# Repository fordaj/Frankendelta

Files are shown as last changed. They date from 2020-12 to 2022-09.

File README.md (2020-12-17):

# Frankendelta
Meet the 45lb, reassembled many times, absolute unit of a Delta 3D Printer: Frankendelta.
~Picture goes here~
Over the summer of 2019, my dad and I worked together to design a 3D printer with a build volume large enough to print my head (that wasn't the main goal... but it's on the list). In all fairness, my dad brought in most of the expertise from building his Kossel Mini Delta 3D printer, scaling up the things he felt worked well from that. I had experience with cartesian printers, but deltas are a different beast. With the right settings, they can print extremely quickly without quality loss due to their light effectors. This repository serves as a medium for functionality and documentation, where I can refer back to the processes and files used to get Frankendelta humming and happy as needed.

## Parts List
Here are most of the parts included in this build. Some not included are the aluminum sheets my dad milled on his CNC, T-nuts, control board standoffs, fans, and supplies (wires, JTX connectors, solder, cables, fuses, etc.). All in all, ended up costing ~$800.
| Quantity | Type | Item | Price |
|--|--|--|--|
| 1 | Control Board | [BIGTREETECH SKR V1.3 32-bit Smoothie Board with SPI TMC2130 Stepper Drivers](https://www.biqu.equipment/products/pre-sale-bigtreetech-skr-v1-3-smoothieboard-32-bit-open-source-arm-cpu-motherboard-support-uart-model-2004lcd-3d-printer-parts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) | $44.95 |
| 1 | Power Supply | [Meanwell 24V, 200W PSU](https://www.aliexpress.com/item/32855960682.html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,searchweb201602_9_10065_10130_10068_10890_10547_319_10546_317_10548_10545_10696_453_10084_454_10083_10618_10307_537_536_10059_10884_10887_321_322_10103,searchweb201603_35,ppcSwitch_0&algo_expid=8e751027-f404-431d-9236-467e57eb0355-0&algo_pvid=8e751027-f404-431d-9236-467e57eb0355&transAbTest=ae803_3) | $32.30 |
| 1 | LCD | [MKS 12864LCD](https://www.amazon.com/HiLetgo-Printer-Controller-Display-Arduino/dp/B07X378P8X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) | $12.99 |
| 4 | Stepper Motors | [NEMA 17 0.9 deg 76oz.in Steppers](https://www.seemecnc.com/collections/parts-accessories/products/nema-17-stepper-motor-1-8-degree-76oz-in-2a-5mm-shaft-w-flat) | $22.50 |
| 7 | Belts | [GT2 x 6mm Wide Timing Belt (sold per meter)](https://www.seemecnc.com/collections/parts-accessories/products/gt2-timing-belt) | $45.50 |
| 1 | Bed Heater| [Circular Silicone Bed Heater 120v, 300mm, 350W](https://www.seemecnc.com/collections/parts-accessories/products/silicone-heater-for-300mm-diameter-beds) | $40.00 |
| 1 | Build Plate | [310mm Circular Glass Build Plate](https://www.seemecnc.com/collections/parts-accessories/products/boroscillicate-glass-build-plate-310mm) | $30.00 |
| 1 | Extruder | [EZR Struder](https://www.seemecnc.com/collections/parts-accessories/products/ezrstruder) | $35.00 |
| 1 | Relay | [Solid State Relay (SSR) 24V~480VAC, 40A, 3-32VDC Control](https://docs.google.com/spreadsheets/d/126paPdKw47GO45m8PfAj-qZeEyYEzkp5sGYM6t5eCeo/edit#gid=2045847217) | $25.00 |
| 3 | Timing Pulley | [16 Tooth Timing Pulley for GT2 x 6mm Belt](https://www.seemecnc.com/collections/parts-accessories/products/16-tooth-g-series-2mm-pitch-x-6mm-wide-timing-pulley-3-pack) | $3.50 |
| 1 | Bed Thermistor | [100k Glass Bead NTC Thermistor](https://www.seemecnc.com/collections/parts-accessories/products/thermistor-100k-ntc) | $6.00 |
| 1 | PTFE Tube | [2mm ID x 4mm OD PTFE Tubing, 7ft](https://www.seemecnc.com/collections/parts-accessories/products/ptfe-tubing-2mm-id-x-4mm-od) | $2.70 |
| 1 | Kossel Delta Corners | [2040 Aluminum Alloy Delta Angle Corner Kit, Kossel XL Update](https://www.aliexpress.com/item/32811135341.html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,searchweb201602_9_10065_10130_10068_10890_10547_319_10546_317_10548_10545_10696_453_10084_454_10083_10618_10307_537_536_10059_10884_10887_321_322_10103,searchweb201603_35,ppcSwitch_0&algo_expid=a3b4f901-13f0-4ec3-b1fd-ec0813078da3-0&algo_pvid=a3b4f901-13f0-4ec3-b1fd-ec0813078da3&transAbTest=ae803_3) | $63.99 |
| 3 | Linear Rails | [600mm MGN9 C Linear Rails with Sliding Carriage](https://www.aliexpress.com/item/3D-print-parts-cnc-Kossel-Mini-MGN9-9mm-miniature-linear-rail-slide-1pc-MGN9-linear-rail/32806622073.html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,searchweb201602_9_10065_10130_10068_10890_10547_319_10546_317_10548_10545_10696_453_10084_454_10083_10618_10307_537_536_10059_10884_10887_321_322_10103,searchweb201603_35,ppcSwitch_0&algo_expid=1050dd04-ff44-4791-b0d4-8a9743b34de0-0&algo_pvid=1050dd04-ff44-4791-b0d4-8a9743b34de0&transAbTest=ae803_3) | $59.49 |
| 1 | Probe | [Duet IR Auto-Bed Leveling Probe](https://www.printedsolid.com/products/duet-ir-probe) | $24.85 |
| 1 | Hotend | [E3D V6 24V Bowden All-Metal Hotend](https://e3d-online.com/collections/hotends/products/v6-all-metal-hotend) | $53.50 |
| 1 | Linear Rails | [V-Slot 20mm x 60mm x 500mm Linear Rail, Black](https://openbuildspartstore.com/v-slot-20x60-linear-rail/) | $10.99 |
| 3 | Linear Rails | [V-Slot 20mm x 40mm x 1000mm Linear Rail, Black](https://openbuildspartstore.com/v-slot-20x40-linear-rail/) | $45.87 |
| 3 | Linear Rails | [V-Slot 20mm x 40mm x 500mm Linear Rail, Black](https://openbuildspartstore.com/v-slot-20x40-linear-rail/) | $23.97 |
| 3 | Linear Rails | [V-Slot 20mm x 40mm x 500mm Linear Rail, Black](https://openbuildspartstore.com/v-slot-20x20-linear-rail/) | $17.97 |

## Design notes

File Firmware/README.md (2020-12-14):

# Marlin Firmware
[Marlin firmware](https://marlinfw.org) version 2.0.7.2, last built 12-14-2020 in [firmware.bin](firmware.bin)

## Configuration.h
All of the changes I've made to the [Configuration.h](Marlin/Configuration.h) file. Since I am using a delta printer, I started with the generic example in [Marlin's configuration repository](https://github.com/MarlinFirmware/Configurations). Sections correspond with order of appearance in files. Actual code shown for simpler CTRL+f navigation.

### Setup
Shows up on host during boot and M115
```cpp
#define STRING_CONFIG_H_AUTHOR "Andrew Ford"
```
Default to serial port 0, otherwise emulate
```cpp
#define SERIAL_PORT 0
#define SERIAL_PORT_2 -1
```
Define motherboard (using BigTreeTech SKR V1.3)
```cpp
#define MOTHERBOARD BOARD_BTT_SKR_V1_3
```
Set printer name
```cpp
#define CUSTOM_MACHINE_NAME "Frankendelta"
```
Disable power supply unit control
```cpp
//#define PSU_CONTROL
```

### Thermistors
Hotend thermistor selection
```cpp
#define TEMP_SENSOR_0 5
```
Bed thermistor selection
```cpp
#define TEMP_SENSOR_BED 1
```

### PID Settings
Auto-tune menu on LCD
```cpp
#define PID_AUTOTUNE_MENU
```
Since I only have 1 hotend, I can set global PID settings
```cpp
#define DEFAULT_Kp 24.43
#define DEFAULT_Ki 1.93
#define DEFAULT_Kd 77.53
```
Use PID settings for bed. Limit heating so that adhesive doesn't melt
```cpp
#define PIDTEMPBED

#define MAX_BED_POWER 200

#define DEFAULT_bedKp 164.97
#define DEFAULT_bedKi 27.02
#define DEFAULT_bedKd 671.52
```

### Delta Settings
After homing, move downwards to prevent overshooting homing sensors
```cpp
#define DELTA_HOME_TO_SAFE_ZONE
```
Allow user to define safe zone
```cpp
#define DELTA_CALIBRATION_MENU
```
Allow G33 Auto-Calibration (used in [calibration file](https://github.com/fordaj/Frankendelta/blob/main/Calibration/calibrateDelta.gcode))
```cpp
#define DELTA_AUTO_CALIBRATION
```
Printable radius(mm) = diameter/2 - unreachable space
```cpp
#define DELTA_PRINTABLE_RADIUS 150.0
```
Diagonal push-rod length
```cpp
#define DELTA_DIAGONAL_ROD 360.24 
```
Printable height (obtained from [calibration file](https://github.com/fordaj/Frankendelta/blob/main/Calibration/calibrateDelta.gcode))
```cpp
#define DELTA_HEIGHT 535.26
```
Endstop adjustment (obtained from [calibration file](https://github.com/fordaj/Frankendelta/blob/main/Calibration/calibrateDelta.gcode))
```cpp
#define DELTA_ENDSTOP_ADJ { 0.0, -0.26, -2.10 }
```
Diagonal push-rod horizontal coverage with centered effector(obtained from [calibration file](https://github.com/fordaj/Frankendelta/blob/main/Calibration/calibrateDelta.gcode))
```cpp
#define DELTA_RADIUS 186.95
```
Tower angle trim
```cpp
#define DELTA_TOWER_ANGLE_TRIM { 0.24, -0.10, -0.14 }
```
Delta radius/diagonal rod adjustments
```cpp
#define DELTA_DIAGONAL_ROD_TRIM_TOWER { 0.0, 0.0, 0.0 }
```

### Endstop Settings
Disable endstop pullups
```cpp
//#define ENDSTOPPULLUPS
```
Ensure endstops are non-inverting
```cpp
#define X_MIN_ENDSTOP_INVERTING false
#define Y_MIN_ENDSTOP_INVERTING false
#define Z_MIN_ENDSTOP_INVERTING false
#define X_MAX_ENDSTOP_INVERTING false
#define Y_MAX_ENDSTOP_INVERTING false
#define Z_MAX_ENDSTOP_INVERTING false
#define Z_MIN_PROBE_ENDSTOP_INVERTING false
```
Enable stepper drivers
```cpp
#define X_DRIVER_TYPE  TMC2130
#define Y_DRIVER_TYPE  TMC2130
#define Z_DRIVER_TYPE  TMC2130

#define E0_DRIVER_TYPE TMC2130
```

### Movement Settings
Adjust "Axis Steps Per Unit" variables
```cpp
#define XYZ_FULL_STEPS_PER_ROTATION 400

#define XYZ_PULLEY_TEETH 16

#define DEFAULT_AXIS_STEPS_PER_UNIT { DEFAULT_XYZ_STEPS_PER_UNIT, DEFAULT_XYZ_STEPS_PER_UNIT, DEFAULT_XYZ_STEPS_PER_UNIT, 158 } 
```
Increase max hotend feedrate
```cpp
#define DEFAULT_MAX_FEEDRATE { 500, 500, 500, 150 }
```
Lower default acceleration
```cpp
#define DEFAULT_ACCELERATION 2000
```
Change default hotend jerk
```cpp
#define DEFAULT_ACCELERATION 2000
```

### Z-Probe Options
Since we are using a laser probe, no mechanical deployment is needed
```cpp
#define FIX_MOUNTED_PROBE
```
Adjust nozzle-to-probe offset
```cpp
#define NOZZLE_TO_PROBE_OFFSET { 0, -19, -2.40 }
```
Define gap between probe locations and bed edge
```cpp
#define PROBING_MARGIN 40
```
Set probe XY movement speed to 100mm/s
```cpp
#define XY_PROBE_SPEED (100*60)
```
Enable multi-probing for improved accuracy
```cpp
#define MULTIPLE_PROBING 2
```
Adjust z-clearances
```cpp
#define Z_CLEARANCE_DEPLOY_PROBE   20
#define Z_CLEARANCE_BETWEEN_PROBES  8
#define Z_CLEARANCE_MULTI_PROBE     5
```
Enable minimum software endstops
```cpp
#define MIN_SOFTWARE_ENDSTOPS
```

### Bed Leveling
Enable 3-point bed leveling since I have a glass bed
```cpp
#define AUTO_BED_LEVELING_3POINT
```
If there is bed level data stored, load it after every [bed leveling](https://github.com/fordaj/Frankendelta/blob/main/Calibration/levelBed.gcode)
```cpp
#define RESTORE_LEVELING_AFTER_G28
```
Set homing speed to 50mm/s
```cpp
#define HOMING_FEEDRATE_Z  (60*60)
```

### Additional Features
Enable EEPROM
```cpp
#define EEPROM_SETTINGS
```
Setup heating profiles
```cpp
#define PREHEAT_1_LABEL       "PLA"
#define PREHEAT_1_TEMP_HOTEND  220
#define PREHEAT_1_TEMP_BED      80
#define PREHEAT_1_FAN_SPEED      0

#define PREHEAT_2_LABEL       "ABS"
#define PREHEAT_2_TEMP_HOTEND  240
#define PREHEAT_2_TEMP_BED      90
#define PREHEAT_2_FAN_SPEED      0
```
Track total/successful/failed/time remaining
```cpp
#define PRINTCOUNTER
```
Enable SD card support
```cpp
#define SDSUPPORT
```
I lost the menu knob orientation coin flip :-)
```cpp
#define REVERSE_ENCODER_DIRECTION
```

### LCD Settings
Choose model
```cpp
#define REPRAP_DISCOUNT_FULL_GRAPHIC_SMART_CONTROLLER
```

### Extra Features
Drive fan with software PWM, which is less annoying than hardware
```cpp
#define FAN_SOFT_PWM
```

## Configuration_adv.h
All of the changes I've made to the [Configuration_adv.h](Marlin/Configuration_adv.h) file. 

### Thermal Settings
Set minimum fan PWM
```cpp
#define FAN_MIN_PWM 35
```
### Additional Features
Sort files alphabetically
```cpp
#define SDCARD_SORT_ALPHA
```
Scroll long filenames
```cpp
#define SCROLL_LONG_FILENAMES
```
Add frames for fan animation, show heating progress bars
```cpp
#define STATUS_FAN_FRAMES 3
#define STATUS_HEAT_PERCENT 
```
Enable babystepping. Make it always available, accessible with a double-click of the knob. Operate in mm instead of microsteps. Move 0.001 per knob click. Combine babystepping and "M851 Z", the probe offset command
```cpp
#define BABYSTEPPING

#define BABYSTEP_ALWAYS_AVAILABLE

#define BABYSTEP_MILLIMETER_UNITS
#define BABYSTEP_MULTIPLICATOR_Z  0.001
#define BABYSTEP_MULTIPLICATOR_XY 0.001 

#define DOUBLECLICK_FOR_Z_BABYSTEPPING

#define BABYSTEP_ZPROBE_OFFSET
```
Configure linear advance
```cpp
#define LIN_ADVANCE

#define LIN_ADVANCE_K 0.3
```
Disable arc support to save memory
```cpp
//#define ARC_SUPPORT
```

### Buffers
Enable firmware/LCD controlled retraction
```cpp
#define FWRETRACT
```
Trinamic Configuration
```cpp
#define HOLD_MULTIPLIER    0.4

#define X_CURRENT       700
#define Y_CURRENT       700
#define Z_CURRENT       700
#define E0_CURRENT      1050

#define TMC_USE_SW_SPI

//#define STEALTHCHOP_E

#define MONITOR_DRIVER_STATUS
```

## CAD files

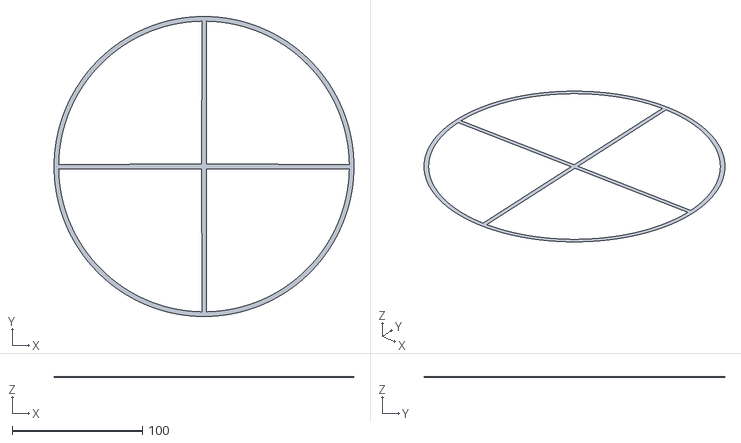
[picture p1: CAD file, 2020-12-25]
Calibration/firstLayer.stl
230.0 x 230.0 x 0.2

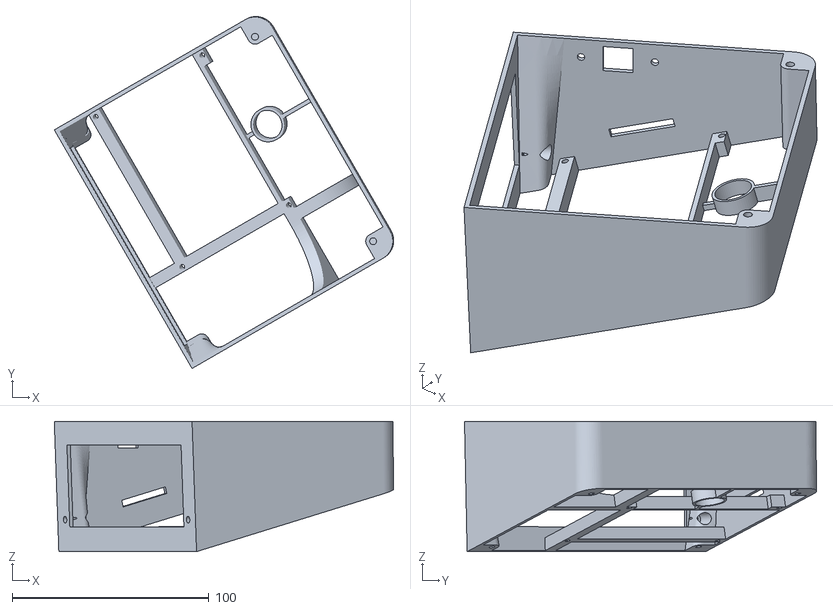
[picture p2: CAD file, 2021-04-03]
Parts/consoleShell.stl
172.5 x 178.9 x 66.2

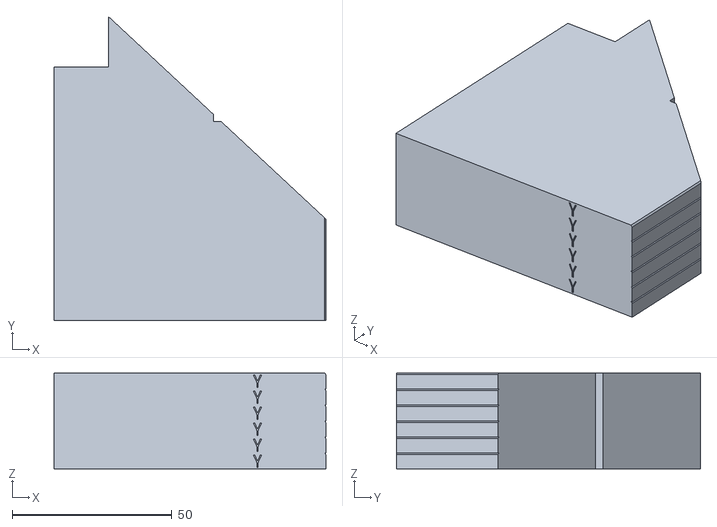
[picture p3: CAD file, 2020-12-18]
Calibration/acceleration.stl
85.0 x 95.0 x 30.0

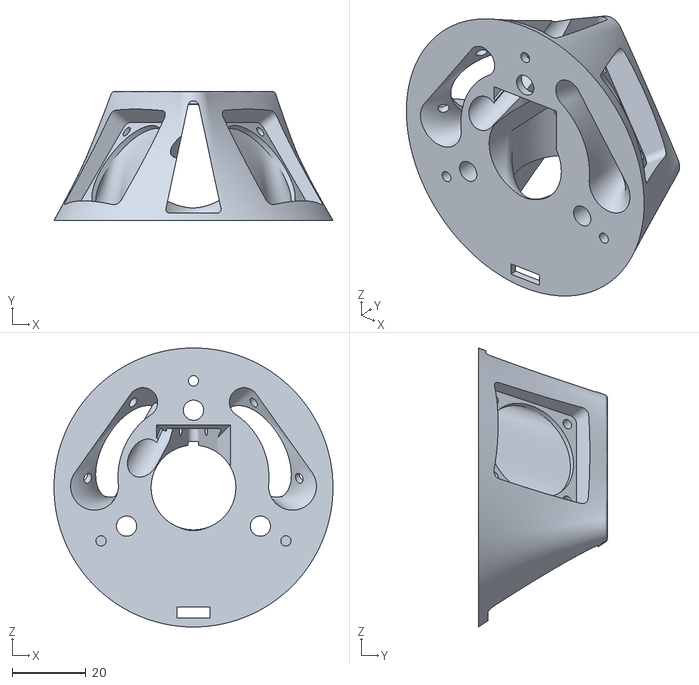
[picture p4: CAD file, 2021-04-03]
Parts/effector.stl
75.8 x 35.0 x 75.8

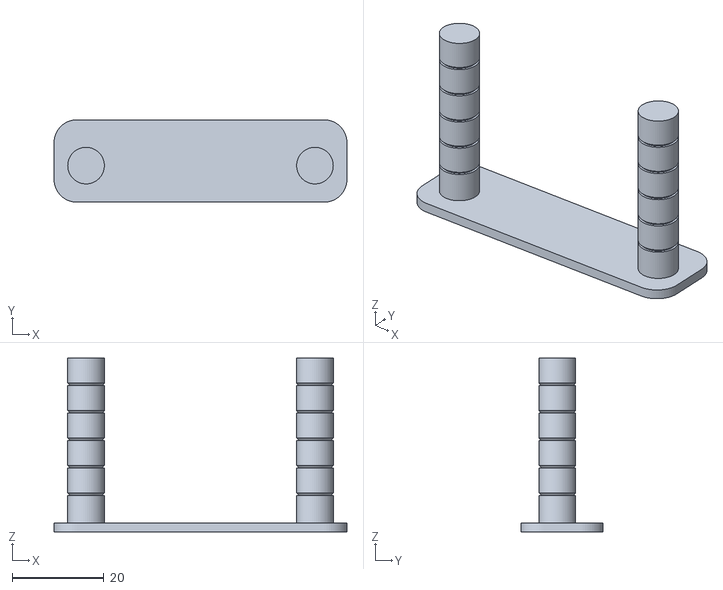
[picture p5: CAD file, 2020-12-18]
Calibration/retraction.stl
64.0 x 18.0 x 38.0

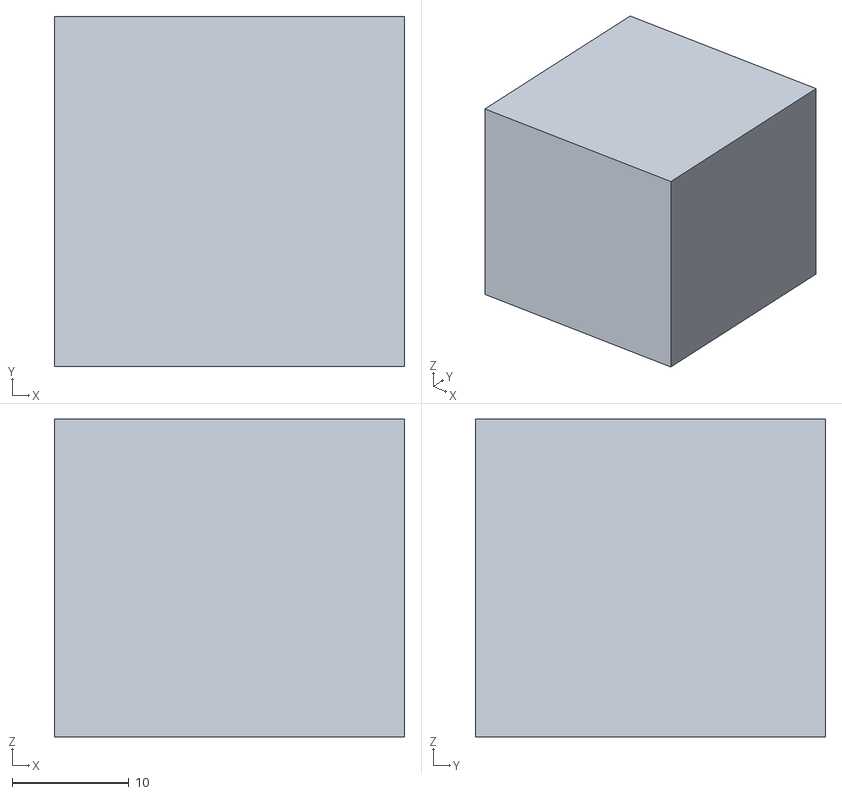
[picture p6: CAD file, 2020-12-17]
Calibration/cube.stl
30.0 x 30.0 x 27.2

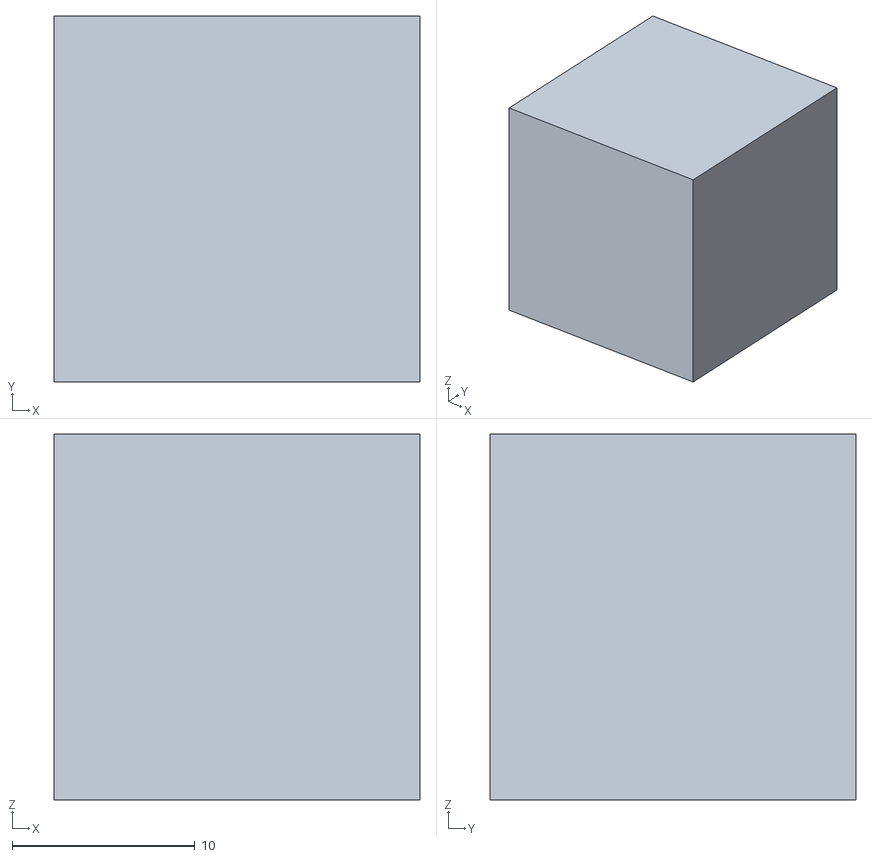
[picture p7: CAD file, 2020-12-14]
Calibration/20mmTestCube.stl
20.0 x 20.0 x 20.0

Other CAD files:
Calibration/20mmTestCube.f3d

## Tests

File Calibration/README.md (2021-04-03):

# Hardware Calibration
Without proper hardware calibration, any software calibration would need corrected. Proper belt tension, stepper bearing alignment, and tight bolts will ensure the printer is reliable.

## Belt Tensioning
1. Choose a frequency meter; I used my iPhone with the <a href="https://apps.apple.com/us/app/easy-tension/id1093873727">Easy Tension</a> application.
2. With the printer off, move the belt carriages halfway down their rails
3. Measure the distance L (cm) from the stepper motor to the pulley
4. To measure belt tension, "pluck" the belt at its midpoint on the non-carriage side. Not so hard that it smacks the rail, but hard enough for the frequency meter to record from 1-3cm away
5. Adjust belt tension until belts match desired frequency f = 3600/L. In my case, f = 3600/98cm = 36.7Hz

# Software Calibration
With the hardware properly tightened/bolted in/connected/configured, we can move onto more precise software calibrations. Should the printer be moved, or print quality suffer, this section will prove useful.

## Probe Z Offset
1. Home the printer (G28)
2. Move the effector Z=1mm away from the bed
3. Using babystepping/0.0025mm adjustment, move Z until the probe sees the bed. Make a note of the Z position when the probe first notices the bed (Z_probe)
4. Take a thin piece of paper and place it under the nozzle. Babystep Z down until it makes contact with the paper, and the paper becomes slightly difficult to move
5. Z_offset = - abs(Z_probe - Z_current)
6. Homing and then G0 Z0 should place the nozzle on a post-it with exactly the pressure you calibrated it to

## Delta Calibration
Lots of data gathered here can be added to the [firmware](https://github.com/fordaj/Frankendelta)
1. Clean the bed of any dirt/dust/plastic etc.
2. Preheat to printing temperatures (ex. [heatPLA.gcode](heatPLA.gcode))
3. Run [calibrateDelta.gcode](calibrateDelta.gcode). This runs G33 (tower calibration), M500 (saves settings), G29 (auto-bed level), M500.

## PID Tuning
Any changes affecting the thermals of the printer should be followed with appropriate PID tuning. Installing a new glass bed, new heat break, fans, nozzle material, etc. all impact the printer's heating rates.
### Hotend
PID auto-tuning for the hotend can be run with M303 from host software (pronterface, octoprint, etc):
```gcode
M303 E0 S220 C15    ; Auto-tune PID values for hotend with 15 cycles 0C to 220C
```
After completion, be sure to copy the new values into Configuration.h. The values can be saved to the printer without rebuilding firmware:
```gcode
M301 P24.76 I1.91 D80.16  ; Write new PID values to EEPROM
M500                        ; Store settings
M501                        ; Load settings
```
Common issues:
1. **No silicone sock on the heater block**: Since the Ender 3 fan blows onto the entire hotend, it prevents the heater block from reaching temperature.
2. **Faulty thermistor/connection/wrong thermistor number in Marlin**: The temperature varies wildly.
3. **Faulty heater cartridge/connection**: Unable to heat up/heats intermittently.
4. **PID settings aren't enabled in Marlin**: Will show up as "Bad extruder number!" when running commands.

### Bed
PID auto-tuning for the bed can be run with an M304:
```gcode
M303 E-1 S80    ; Auto-tune PID values for bed with 5 cycles 0C to 60C
```
After completion, be sure to copy the new values into Configuration.h. The values can be saved to the printer without rebuilding firmware:
```gcode
M304 P99.85 I11.14 D596.73  ; Write new PID values to EEPROM
M500                        ; Store settings
M501                        ; Load settings
```

## Bed Leveling
To calibrate the saved mesh in UBL, run [UBL.gcode](UBL.gcode):
```gcode
M502            ; Load firmware settings
M500            ; Store settings in EEPROM
M501            ; Load settings from EEPROM
M190 S80        ; Heat bed to 80
M104 S220       ; Heat nozzle to 220
G28             ; Home
G29 P1          ; Probe the bed
G29 P3 T        ; Repeat until all mesh points are filled in
G29 S1          ; Save UBL mesh points to EEPROM
G29 F 10.0      ; Set Fade Height for correction at 10.0 mm
G29 A           ; Activate the UBL
M500            ; Store settings
M501            ; Load settings
```
Code modified from Marlin's [documentation](https://marlinfw.org/docs/features/unified_bed_leveling.html). Before every print, the mesh can be verified and tilted with a 3-point bed level:
```gcode
G29 L1  ; Load the mesh saved in slot 1
G29 J   ; 3-point ABL, tilt mesh accordingly
```

## E-steps
1. Heat the nozzle to the temperature you'll be printing with
2. Put the printer in relative position, and print out the old e-step value
```gcode
G91 ; Relative positioning
M92 ; The "E" parameter is the old e-step value
```
3. Mark the filament with a marker as close to the extruder as possible
4. Make another mark on the incoming filament 120mm away from the first mark
5. Turn the extruder knob to push filament through the hotend until your first mark lines up with the beginning of the extruder
6. Extrude 100mm of filament
```gcode
G1 E100 F50    ; Extrude 100mm of filament at 50mm/s
```
7. New_ESteps = Old_ESteps * 100 / (120 - length_remaining) (Teaching Teach offers an [e-step calculator](https://teachingtechyt.github.io/calibration.html#esteps))
8. Write New_ESteps to the printer
```gcode
M92 E192 ; Write e-steps to printer
M500     ; Store settings
M501     ; Load settings
```
8. Repeat steps 3-7 until the length_remaining is 20mm
At this point, many tutorials have you adjust your slicer's flow rate multiplier. I don't like to do this, because if the e-steps are tuned and the hotend is assembled correctly, then this should not be changed. To verify that you've properly calibrated your e-steps, print [cube.gcode](cube.gcode) and ensure that the edges are 0.40mm wide.

## Retraction
I used a [retraction tower](retraction.gcode) from using Teaching Tech's [online generator](https://teachingtechyt.github.io/calibration.html#retraction).

## Acceleration and Jerk
I used an [acceleration test](acceleration.gcode) from using Teaching Tech's [online generator](https://teachingtechyt.github.io/calibration.html#accel).

## Linear Advance
I used [linearAdvance](linearAdvance.gcode) from Marlin's linear advance [gcode generator](https://marlinfw.org/tools/lin_advance/k-factor.html). Note: For whatever reason, the code took *3 minutes* to get from home position to the bed.

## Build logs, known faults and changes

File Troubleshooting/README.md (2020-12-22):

# Duet Infrared Probe
The runner-up candidate of names for this printer would be "Probe Eater" or "Probe Toaster". I've ordered *three* of these [Duet IR Probes](https://www.printedsolid.com/products/duet-ir-probe) for $25 + shipping... and my best guess is that this circuit is not shielded from over-voltage/current conditions. As of 12/22/2020, I fried their V1.3 board when pressing the reset button on my printer to flash a new Marlin build. *This is a working theory, and I will no longer be using the reset button to see if it fries the next probe*. I am switching to this [clone](https://www.amazon.com/gp/product/B07RKTQ53F/ref=ppx_yo_dt_b_asin_title_o01_s00?ie=UTF8&psc=1), which is $15.

### Fried Infrared Transmitter 
- Probe properly blinks 2 times a few seconds after power-on
- Probe does not sense bed/finger/other objects
- Probe IR transmitter is not picked up by digital (phone) camera
- Probe can receive IR transmission from TV remotes, and will illuminate its LED accordingly

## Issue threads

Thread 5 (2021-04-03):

Stringing mid print

fordaj, 2021-04-03:
- calibrate retraction settings
- Fix flow rate

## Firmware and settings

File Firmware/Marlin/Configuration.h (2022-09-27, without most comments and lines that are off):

#pragma once
#define CONFIGURATION_H_VERSION 020007
#define STRING_CONFIG_H_AUTHOR "Andy Ford, Frankendelta, BTT-1.4 Turbo" // Who made the changes.
#define SHOW_BOOTSCREEN
#define SHOW_CUSTOM_BOOTSCREEN
#define CUSTOM_STATUS_SCREEN_IMAGE
#define SERIAL_PORT -1
#define SERIAL_PORT_2 0
#define BAUDRATE 115200
  #define MOTHERBOARD BOARD_BTT_SKR_V1_4_TURBO
#define CUSTOM_MACHINE_NAME "Frankendelta"
#define EXTRUDERS 1
#define DEFAULT_NOMINAL_FILAMENT_DIA 1.75
#define PSU_NAME "Power Supply"
#define TEMP_SENSOR_0 5
#define TEMP_SENSOR_1 0
#define TEMP_SENSOR_2 0
#define TEMP_SENSOR_3 0
#define TEMP_SENSOR_4 0
#define TEMP_SENSOR_5 0
#define TEMP_SENSOR_6 0
#define TEMP_SENSOR_7 0
#define TEMP_SENSOR_BED 1
#define TEMP_SENSOR_PROBE 0
#define TEMP_SENSOR_CHAMBER 0
#define DUMMY_THERMISTOR_998_VALUE 25
#define DUMMY_THERMISTOR_999_VALUE 100
#define MAX_REDUNDANT_TEMP_SENSOR_DIFF 10
#define TEMP_RESIDENCY_TIME     10  // (seconds) Time to wait for hotend to "settle" in M109
#define TEMP_WINDOW              1  // (°C) Temperature proximity for the "temperature reached" timer
#define TEMP_HYSTERESIS          3  // (°C) Temperature proximity considered "close enough" to the target
#define TEMP_BED_RESIDENCY_TIME  0  // (seconds) Time to wait for bed to "settle" in M190
#define TEMP_BED_WINDOW          1  // (°C) Temperature proximity for the "temperature reached" timer
#define TEMP_BED_HYSTERESIS      3  // (°C) Temperature proximity considered "close enough" to the target
#define HEATER_0_MINTEMP   5
#define HEATER_1_MINTEMP   5
#define HEATER_2_MINTEMP   5
#define HEATER_3_MINTEMP   5
#define HEATER_4_MINTEMP   5
#define HEATER_5_MINTEMP   5
#define HEATER_6_MINTEMP   5
#define HEATER_7_MINTEMP   5
#define BED_MINTEMP        5
#define HEATER_0_MAXTEMP 275
#define HEATER_1_MAXTEMP 275
#define HEATER_2_MAXTEMP 275
#define HEATER_3_MAXTEMP 275
#define HEATER_4_MAXTEMP 275
#define HEATER_5_MAXTEMP 275
#define HEATER_6_MAXTEMP 275
#define HEATER_7_MAXTEMP 275
#define BED_MAXTEMP      150
#define PIDTEMP
#define BANG_MAX 255     // Limits current to nozzle while in bang-bang mode; 255=full current
#define PID_MAX BANG_MAX // Limits current to nozzle while PID is active (see PID_FUNCTIONAL_RANGE below); 255=full current
#define PID_K1 0.95      // Smoothing factor within any PID loop
  #define PID_AUTOTUNE_MENU     // Add PID auto-tuning to the "Advanced Settings" menu. (~250 bytes of PROGMEM)
    #define DEFAULT_Kp 25.37
    #define DEFAULT_Ki 1.98
    #define DEFAULT_Kd 81.35
#define PIDTEMPBED
#define MAX_BED_POWER 200 // limits duty cycle to bed; 255=full current
  #define DEFAULT_bedKp 87.99
  #define DEFAULT_bedKi 9.73
  #define DEFAULT_bedKd 530.22
  #define PID_FUNCTIONAL_RANGE 10 // If the temperature difference between the target temperature and the actual temperature
#define PREVENT_COLD_EXTRUSION
#define EXTRUDE_MINTEMP 170
#define PREVENT_LENGTHY_EXTRUDE
#define EXTRUDE_MAXLENGTH 801 // High for filament change retract
#define THERMAL_PROTECTION_HOTENDS // Enable thermal protection for all extruders
#define THERMAL_PROTECTION_BED     // Enable thermal protection for the heated bed
#define THERMAL_PROTECTION_CHAMBER // Enable thermal protection for the heated chamber
#define DELTA
  #define DELTA_SEGMENTS_PER_SECOND 160 //200
  #define DELTA_HOME_TO_SAFE_ZONE
  #define DELTA_CALIBRATION_MENU
  #define DELTA_AUTO_CALIBRATION
    #define DELTA_CALIBRATION_DEFAULT_POINTS 4
    #define PROBE_MANUALLY_STEP 0.05      // (mm)
  #define DELTA_PRINTABLE_RADIUS 150.0    // (mm)
  #define DELTA_DIAGONAL_ROD 360.24        // (mm)
  #define DELTA_HEIGHT 531.94             // (mm) Get this value from G33 auto calibrate
  #define DELTA_ENDSTOP_ADJ { -0.47, 0, -0.54 } // Get these values from G33 auto calibrate
  #define DELTA_RADIUS 189.01              // (mm) Get this value from G33 auto calibrate
  #define DELTA_TOWER_ANGLE_TRIM { 0.20, -0.15, -0.05 } // Get these values from G33 auto calibrate
  #define DELTA_DIAGONAL_ROD_TRIM_TOWER { 0.0, 0.0, 0.0 }
#define USE_ZMIN_PLUG // a Z probe
#define USE_XMAX_PLUG
#define USE_YMAX_PLUG
#define USE_ZMAX_PLUG
  #define ENDSTOPPULLUP_XMAX
  #define ENDSTOPPULLUP_YMAX
  #define ENDSTOPPULLUP_ZMAX
  #define ENDSTOPPULLUP_ZMIN
#define X_MIN_ENDSTOP_INVERTING false  // Set to true to invert the logic of the endstop.
#define Y_MIN_ENDSTOP_INVERTING false  // Set to true to invert the logic of the endstop.
#define Z_MIN_ENDSTOP_INVERTING false  // Set to true to invert the logic of the endstop.
#define X_MAX_ENDSTOP_INVERTING false  // Set to true to invert the logic of the endstop.
#define Y_MAX_ENDSTOP_INVERTING false  // Set to true to invert the logic of the endstop.
#define Z_MAX_ENDSTOP_INVERTING false  // Set to true to invert the logic of the endstop.
#define Z_MIN_PROBE_ENDSTOP_INVERTING false  // Set to true to invert the logic of the probe.
#define X_DRIVER_TYPE  TMC2209 //TMC2130
#define Y_DRIVER_TYPE  TMC2209 //TMC2130
#define Z_DRIVER_TYPE  TMC2209 //TMC2130
#define E0_DRIVER_TYPE TMC2209 //TMC2130
#define XYZ_FULL_STEPS_PER_ROTATION 400
#define XYZ_MICROSTEPS 16
#define XYZ_BELT_PITCH 2
#define XYZ_PULLEY_TEETH 16
#define DEFAULT_XYZ_STEPS_PER_UNIT ((XYZ_FULL_STEPS_PER_ROTATION) * (XYZ_MICROSTEPS) / double(XYZ_BELT_PITCH) / double(XYZ_PULLEY_TEETH)) + 2
#define DEFAULT_AXIS_STEPS_PER_UNIT   { DEFAULT_XYZ_STEPS_PER_UNIT, DEFAULT_XYZ_STEPS_PER_UNIT, DEFAULT_XYZ_STEPS_PER_UNIT, 185 }  // SeeMeCNC
#define DEFAULT_MAX_FEEDRATE          { 500, 500, 500, 50 } // E: 150
#define DEFAULT_MAX_ACCELERATION      { 9000, 9000, 9000, 10000 }
#define DEFAULT_ACCELERATION          2000    // X, Y, Z and E acceleration for printing moves
#define DEFAULT_RETRACT_ACCELERATION  3000    // E acceleration for retracts
#define DEFAULT_TRAVEL_ACCELERATION   3000    // X, Y, Z acceleration for travel (non printing) moves
#define CLASSIC_JERK
  #define DEFAULT_XJERK 10.0
  #define DEFAULT_YJERK DEFAULT_XJERK
  #define DEFAULT_ZJERK DEFAULT_XJERK // Must be same as XY for delta
#define DEFAULT_EJERK    20.0  // May be used by Linear Advance
#define Z_MIN_PROBE_PIN P1_26 // Pin 32 is the RAMPS default
#define FIX_MOUNTED_PROBE
#define NOZZLE_TO_PROBE_OFFSET { 0, -19, -2.390 } // 03-29-2021
#define PROBING_MARGIN 30
#define XY_PROBE_SPEED (100*60)
#define Z_PROBE_SPEED_FAST HOMING_FEEDRATE_Z
#define Z_PROBE_SPEED_SLOW (Z_PROBE_SPEED_FAST / 2)
#define MULTIPLE_PROBING 2
#define EXTRA_PROBING    1
#define Z_CLEARANCE_DEPLOY_PROBE   20 // Z Clearance for Deploy/Stow
#define Z_CLEARANCE_BETWEEN_PROBES  8 // Z Clearance between probe points
#define Z_CLEARANCE_MULTI_PROBE     5 // Z Clearance between multiple probes
#define Z_PROBE_LOW_POINT          -2 // Farthest distance below the trigger-point to go before stopping
#define Z_PROBE_OFFSET_RANGE_MIN -20
#define Z_PROBE_OFFSET_RANGE_MAX 20
#define X_ENABLE_ON 0
#define Y_ENABLE_ON 0
#define Z_ENABLE_ON 0
#define E_ENABLE_ON 0 // For all extruders
#define DISABLE_X false
#define DISABLE_Y false
#define DISABLE_Z false
#define DISABLE_E false             // Disable the extruder when not stepping
#define DISABLE_INACTIVE_EXTRUDER   // Keep only the active extruder enabled
#define INVERT_X_DIR false
#define INVERT_Y_DIR false
#define INVERT_Z_DIR false
#define INVERT_E0_DIR false
#define INVERT_E1_DIR false
#define INVERT_E2_DIR false
#define INVERT_E3_DIR false
#define INVERT_E4_DIR false
#define INVERT_E5_DIR false
#define INVERT_E6_DIR false
#define INVERT_E7_DIR false
#define X_HOME_DIR 1  // deltas always home to max
#define Y_HOME_DIR 1
#define Z_HOME_DIR 1
#define X_BED_SIZE ((DELTA_PRINTABLE_RADIUS) * 2)
#define Y_BED_SIZE ((DELTA_PRINTABLE_RADIUS) * 2)
#define X_MIN_POS -(DELTA_PRINTABLE_RADIUS)
#define Y_MIN_POS -(DELTA_PRINTABLE_RADIUS)
#define Z_MIN_POS 0
#define X_MAX_POS DELTA_PRINTABLE_RADIUS
#define Y_MAX_POS DELTA_PRINTABLE_RADIUS
#define Z_MAX_POS MANUAL_Z_HOME_POS
#define MAX_SOFTWARE_ENDSTOPS
  #define MAX_SOFTWARE_ENDSTOP_X
  #define MAX_SOFTWARE_ENDSTOP_Y
  #define MAX_SOFTWARE_ENDSTOP_Z
#define AUTO_BED_LEVELING_UBL
#define RESTORE_LEVELING_AFTER_G28
  #define ENABLE_LEVELING_FADE_HEIGHT
  #define SEGMENT_LEVELED_MOVES
  #define LEVELED_SEGMENT_LENGTH 5.0 // (mm) Length of all segments (except the last one)
  #define MESH_INSET  1 //40          // Set Mesh bounds as an inset region of the bed
  #define GRID_MAX_POINTS_X 15 //10   // Don't use more than 15 points per axis, implementation limited.
  #define GRID_MAX_POINTS_Y GRID_MAX_POINTS_X
  #define UBL_MESH_EDIT_MOVES_Z     // Sophisticated users prefer no movement of nozzle
  #define UBL_SAVE_ACTIVE_ON_M500   // Save the currently active mesh in the current slot on M500
#define LCD_BED_LEVELING
  #define MESH_EDIT_Z_STEP  0.025 // (mm) Step size while manually probing Z axis.
  #define LCD_PROBE_Z_RANGE 4     // (mm) Z Range centered on Z_MIN_POS for LCD Z adjustment
#define BED_CENTER_AT_0_0
#define MANUAL_Z_HOME_POS DELTA_HEIGHT // Distance between the nozzle to printbed after homing
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

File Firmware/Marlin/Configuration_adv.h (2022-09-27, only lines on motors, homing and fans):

#define E0_AUTO_FAN_PIN -1
#define E1_AUTO_FAN_PIN -1
#define E2_AUTO_FAN_PIN -1
#define E3_AUTO_FAN_PIN -1
#define E4_AUTO_FAN_PIN -1
#define E5_AUTO_FAN_PIN -1
#define E6_AUTO_FAN_PIN -1
#define E7_AUTO_FAN_PIN -1
#define CHAMBER_AUTO_FAN_PIN -1
#define HOMING_BUMP_MM      { 5, 5, 5 }       // (mm) Backoff from endstops after first bump
#define HOMING_BUMP_DIVISOR { 5, 5, 5 }       // Re-Bump Speed Divisor (Divides the Homing Feedrate)
#define MICROSTEP_MODES { 16, 16, 16, 16, 16, 16 } // [1,2,4,8,16]
#define LIN_ADVANCE
  #define LIN_ADVANCE_K 0.3 //0.7    // Unit: mm compression per 1mm/s extruder speed
#define ADVANCED_PAUSE_FEATURE
  #define ADVANCED_PAUSE_PURGE_FEEDRATE        3  // (mm/s) Extrude feedrate (after loading). Should be slower than load feedrate.
  #define ADVANCED_PAUSE_PURGE_LENGTH         10  // (mm) Length to extrude after loading.
  #define ADVANCED_PAUSE_RESUME_PRIME          0  // (mm) Extra distance to prime nozzle after returning from park.
    #define X_CURRENT      1000        // (mA) RMS current. Multiply by 1.414 for peak current.
    #define X_CURRENT_HOME  X_CURRENT  // (mA) RMS current for sensorless homing
    #define X_MICROSTEPS     16    // 0..256
    #define Y_CURRENT      1000
    #define Y_CURRENT_HOME  Y_CURRENT
    #define Y_MICROSTEPS     16
    #define Z_CURRENT      1000
    #define Z_CURRENT_HOME  Z_CURRENT
    #define Z_MICROSTEPS     16
    #define E0_CURRENT      1000
    #define E0_MICROSTEPS    16
    #define CURRENT_STEP_DOWN     50  // [mA]
    #define REPORT_CURRENT_CHANGE
  #define X_HYBRID_THRESHOLD     100  // [mm/s]
  #define X2_HYBRID_THRESHOLD    100
  #define Y_HYBRID_THRESHOLD     100
  #define Y2_HYBRID_THRESHOLD    100
  #define Z_HYBRID_THRESHOLD     100 // 3
  #define Z2_HYBRID_THRESHOLD      3
  #define Z3_HYBRID_THRESHOLD      3
  #define Z4_HYBRID_THRESHOLD      3
  #define E0_HYBRID_THRESHOLD     40 // 30
  #define E1_HYBRID_THRESHOLD     30
  #define E2_HYBRID_THRESHOLD     30
  #define E3_HYBRID_THRESHOLD     30
  #define E4_HYBRID_THRESHOLD     30
  #define E5_HYBRID_THRESHOLD     30
  #define E6_HYBRID_THRESHOLD     30
  #define E7_HYBRID_THRESHOLD     30

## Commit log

2020-12-14 Added belt tensioning to calibration readme
2020-12-14 Added tower calibration content.
2020-12-14 Elaborated on measuring belt tension
2020-12-14 Added marlin files. Created firmware folder.
    [Configuration.h, Configuration_adv.h]
2020-12-14 Added generic delta config files
    [Configuration.h, Configuration_adv.h]
2020-12-14 Started documenting configuration.h
    [Configuration.h]
2020-12-14 Continued updating config.h
    [Configuration.h]
2020-12-14 Completed configuration.h documentation
    [Configuration.h]
2020-12-14 Documented Configuration_adv.h
    [Configuration_adv.h]
2020-12-14 Built firmware. Corrected configuration errors.
    [Configuration.h, Configuration_adv.h]
2020-12-14 Changed homing approach speed to 50mm/s
    [Configuration.h]
2020-12-14 Adjusted z-probe offset + added calibration notes
    [Configuration.h]
2020-12-14 Added step "clean bed"
2020-12-14 Added test cube
    [20mmTestCube.f3d, 20mmTestCube.stl]
2020-12-14 Run print to ensure proper Z-offset
2020-12-14 Added linear rails to parts list
2020-12-17 Rebuilt delta firmware
    [Configuration.h, Configuration_adv.h, firstLayer.stl]
2020-12-17 Increased mesh inset for UBL
    [Configuration.h]
2020-12-17 Added E-step calibration and UBL
    [Configuration.h, cube.stl]
2020-12-18 Added flow rate section
    [retraction.stl]
2020-12-18 Added acceleration tower
    [acceleration.stl]
2020-12-18 Slowed homing feedrate
    [Configuration.h]
2020-12-18 Slowed baseline speed to 100mm/s
2020-12-18 Added linear advance calibration
2020-12-18 Configured linear advance
    [Configuration_adv.h]
2020-12-20 Removed slicer flow rate section
2020-12-22 Added pio files. Reflashed with bilinear ABL
    [Configuration.h]
2020-12-22 Rebuilt with UBL
    [Configuration.h]
2020-12-22 Added troubleshooting section for IR probe
2020-12-22 Switched to bilinear ABL after replacing IR probe
    [Configuration.h]
2020-12-24 Switched from LCD to Onboard SD
    [Configuration_adv.h]
2020-12-25 Shrank so skirt doesn't cause probe to crash
    [firstLayer.stl]
2021-03-29 Updated E-Step number
    [Configuration.h]
2021-04-03 Swapped to SKR v1.4 Turbo board
    [Configuration.h, Configuration_adv.h, consoleShell.stl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]
2021-04-03 Added extra probe
    [Configuration.h]
2021-04-03 Increased E steps/mm to 185
    [Configuration.h]
2021-04-03 Reduced homing/probing feedrate
    [Configuration.h]
2021-04-03 Added cube to measure the flow
2021-04-03 Added extra probing point
    [Configuration.h]
2021-04-03 Added G33 values
    [Configuration.h]
2021-04-03 Disabled fade height
    [Configuration.h]
2021-04-03 Saved g33 values
    [Configuration.h]
2021-04-04 Reverted e steps/mm to 192
    [Configuration.h]
2021-04-04 Increased TMC driver current to 800mA
    [Configuration_adv.h]
2021-04-04 G33 after adjusting belts
    [Configuration.h]
2022-09-27 Homing bump, filament retract length, UBL file
    [Configuration.h, Configuration_adv.h]

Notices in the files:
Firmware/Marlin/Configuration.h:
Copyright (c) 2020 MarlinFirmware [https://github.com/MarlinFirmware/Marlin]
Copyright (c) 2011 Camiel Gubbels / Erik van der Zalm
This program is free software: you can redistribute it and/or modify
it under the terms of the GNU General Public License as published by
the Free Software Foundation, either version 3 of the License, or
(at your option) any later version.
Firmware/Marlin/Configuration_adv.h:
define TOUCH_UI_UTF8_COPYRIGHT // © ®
